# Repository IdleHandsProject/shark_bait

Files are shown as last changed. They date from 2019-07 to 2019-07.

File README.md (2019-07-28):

# SHARK BAIT

Check out the video using the Shark Bait Pumping System:
Shark Bait Video (https://youtu.be/ugRc5jx80yg)

[Marks Channel](https://www.youtube.com/markrober)

For any questions regarding the project or parts please contact SeanHodginsYT@gmail.com

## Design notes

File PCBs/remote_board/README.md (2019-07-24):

# WIND Breakout

## wind makes the feather fly.

WIND is a breakout board for the Adafruit Feather Series to make it easier to fly wire and put together a project with little to no soldering. 

It contains a battery holder for a 18650(I hate loose batteries!), a few buttons, and 5 pin headers for each pin(plus a proto section). There is a power switch connected to the Enable pin(shuts off the regulator), and a voltage divider to the A0 analog 
for monitoring battery voltage.  

This makes it easy to mount in a housing, and wire up different sensors you want to test.

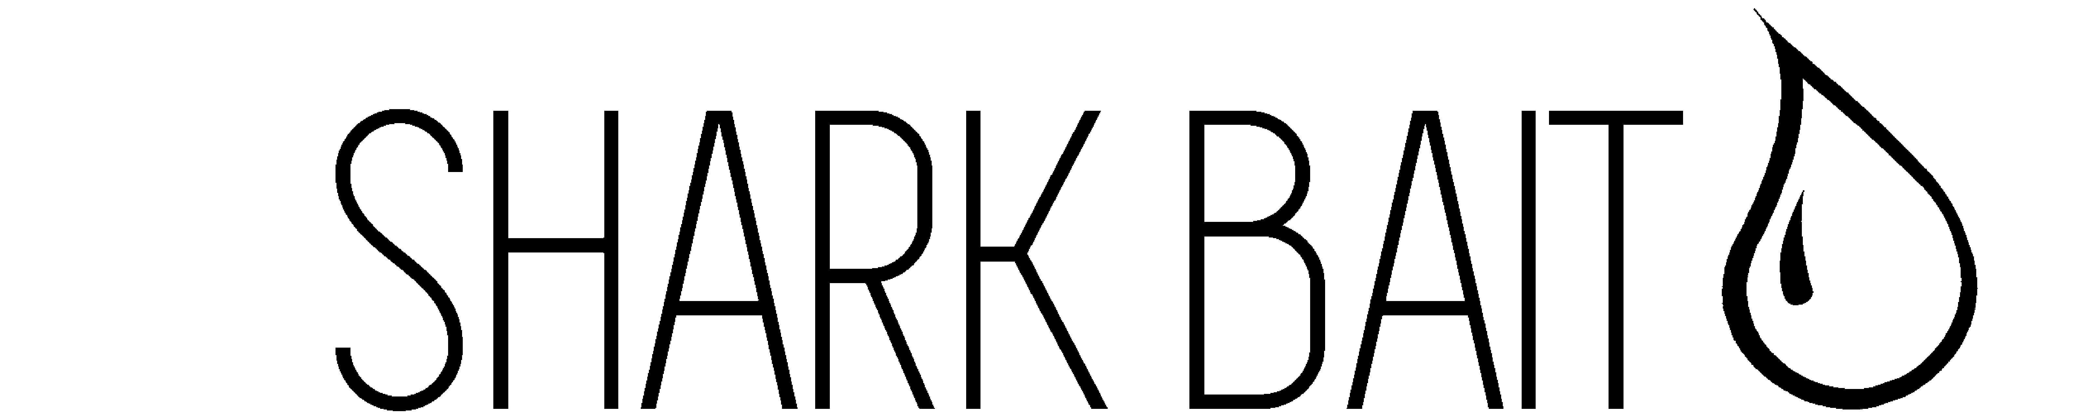
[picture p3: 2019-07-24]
Images/sharkbait.bmp

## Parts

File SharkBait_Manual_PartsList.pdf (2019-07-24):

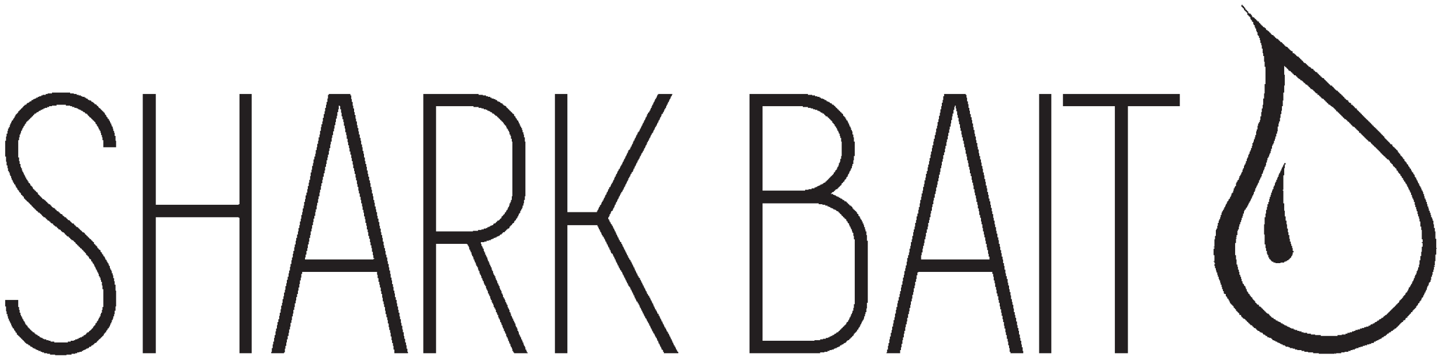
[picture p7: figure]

# Manual and Parts List

## WIRELESS FLUID PUMPING SYSTEM

# PARTS LIST

The following is a list of parts required to build the Shark Bait pumping system. Some parts may vary depending on your requirements.

5 x Adafruit Feather with LoRa - http://bit.ly/sharkbait_feather

4 x Adafruit Motor Wing - http://bit.ly/sharkbait_motor

5 x Waterproof Case - http://bit.ly/sharkbait_case

4 x Peristaltic Pumps 170 ~ 460 mL/min - http://bit.ly/sharkbait_pump

4 x Liquid Container - http://bit.ly/sharkbait_liquid

Silicone 1/4” Tubing - http://bit.ly/sharkbait_tubing

The frames were assembled using various pieces of wood and then mounted to surfboards. You will be required to build your own mounts.

Custom Circuit Boards (Pump and Controller) - Design files available(including BOM), see GitHub link below.

3D Printed Parts - STL Files available in the GitHub link below.

You can find the GitHub that includes the design files and Arduino code here: http://bit.ly/sharkbait_github

For any questions regarding the parts or project, please contact Sean Hodgins. seanhodginsYT@gmail.com

# CONTROLS

## POWER

## ARM

## FLOW SETTINGS

## PRIME

## (REVERSE)

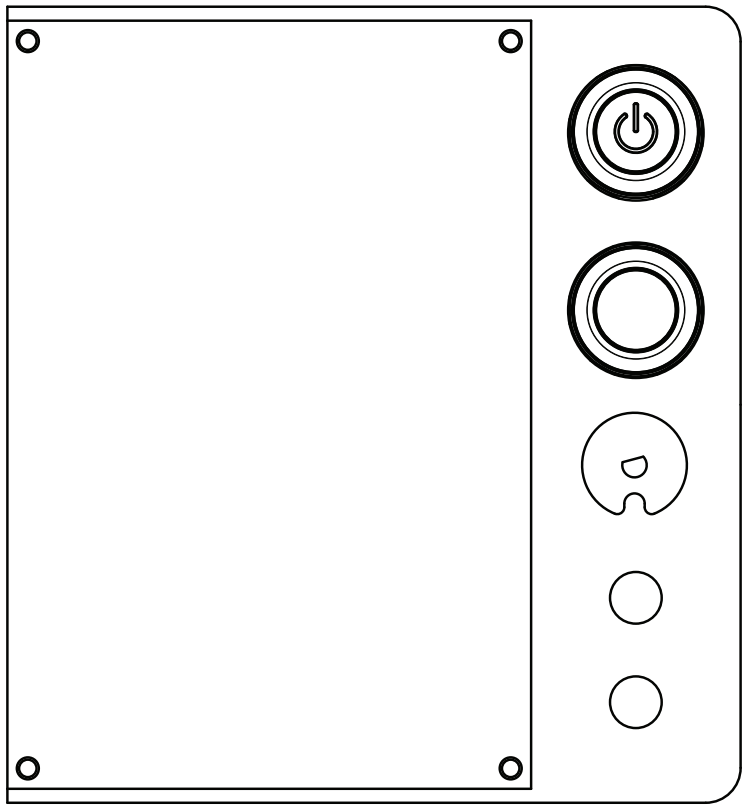
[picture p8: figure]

POWER Button - Direct connection to battery. When in OFF position(UP), no power is provided to the board. POWER button will illuminate when powered.

ARM Button - Will not pump any liquid or respond to remote unless ARM is in ON position(DOWN).

FLOW SETTINGS Knob - 10 settings with an end stop at setting 1(counter clockwise), and 10(clockwise). ARM button illumination will display setting in number of blinks (see next page).

PRIME Button - When held down will cause pump to run forwards(from le port to right port). ARM button will illuminate fully when priming.

REVERSE Button - When held down before holding PRIME will cause the pump to run backwards(from right port to le port). This can be useful for refilling bags(in small amounts).

# SETTINGS

When powering system with ARM Button in the OFF position(UP) system will blink a number of times according to what setting the FLOW Knob is set to (1-10). E.g. Setting 1 will blink once quickly, setting 10 will blink 10 times quickly.

Turn FLOW Knob to desired position coresponding to the flow test amount below. The test amount is in relation to a ONE HOUR test. Each pump of the motor will release approximiately 0.8mL of liquid.
FLOW KNOB SETTING | TEST AMOUNT(mL) | PUMP DELAY(S)
1 | 3.2 900
2 | 25 | 115.2
3 | 50 | 57.6
4 | 100 | 28.8
5 | 250 | 11.5
6 | 500 | 5.8
7 | 750 | 3.8
8 | 1000 | 2.9
9 | 1500 | 1.9
10 | 2000 | 1.4

Once desired flow setting is set, press ARM button to start listening and responding to remote.

ARM button will blink quickly when remote is powered and has received a signal from the remote.

The remote is capable of indicating when the pumps are responding the the signal, and if they are in a pumping state or not.

# MANUAL OVERRIDE

In the rare case the remote is not responding to the pumps, you can put the pumps in MANUAL OVERRIDE mode. This means the pumps will start pumping ONE HOUR aer powering on. Flow rate will be whatever is set at the time the ONE HOUR timer is over. They will not repsond to the remote in MANUAL OVERRIDE mode.

1) First make sure each pump is powered OFF, and ARM button is in OFF Position(UP).

2)Power ON device and select your desired flow setting for each pump.

3) Power OFF device, and set ARM Button to ON Position (DOWN).
4) Power device back ON with ARM button remaining in ON Position. The ARM Button will now blink every second. The flow rate knob can be changed at any time, but no light indication will be available to determine correct setting.
(Its posible to count from one end stop of the knob to the correct position.)

# REMOTE SETTINGS

The remote contains 8 LEDs, 4 LEDs (YELLOW, 5mm) indicate response from the pumps, and 4 LEDs (GREEN, 3mm) indicate an attempt to contact the each pump.

There are two buttons on the side of the remote, POWER and PUMP. The POWER Button will power on the device, the PUMP button will tell any ARMED pumps to begin pumping, when the PUMP button is ON (DOWN).

When the pumps respond to the TX and they are not pumping, the RX LED will blink for that corresponding pump. If the remote PUMP button is ON(down), and the pumps are pumping the RX led will stay illuminated.
The remote will continue to check connectivity to the pumps, and if signal is lost the RX led will turn o. This does not mean the pump has stopped pumping. They will continue to run their test even if the remote is shut o. To stop the motors, turn the PUMP button on the remote to o, while the remote is powered on.
TX | RX/Indication

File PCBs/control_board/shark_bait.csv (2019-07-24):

Id | Designator | Package | Quantity | Designation | Supplier and ref
1 | U4 | SAMD21G18_MOD | 1 | SAMD21_MOD
2 | C2,C4 | C_0402 | 2 | 15pF
3 | C3,C5,C11,C12 | C_0402 | 4 | 0.1uF
4 | C8,C9 | C_0402 | 2 | 1uF
5 | D2 | LED-0603 | 1 | YLED
6 | D1 | LED-0603 | 1 | GLED
7 | R3 | R_0402 | 1 | 10k
8 | R9,R8 | R_0402 | 2 | 1k
9 | Y1 | crystal_smd_3.20x1.50mm2 | 1 | Crystal_Small
10 | D3,D4 | SOD-323 | 2 | BAT20J
11 | J2,J4,J1,J3,J5 | TESTP_1_5 | 5 | TEST_1P
12 | U2 | QFN-48-EP-ST_NoVia | 1 | SAMD21G18
13 | SW4 | switch_kmr2 | 1 | SW_PUSH
14 | U1 | SOT-23-5 | 1 | AP2112K-3.3V
15 | G*** | SH_LOGO_2P5mm | 1 | LOGO

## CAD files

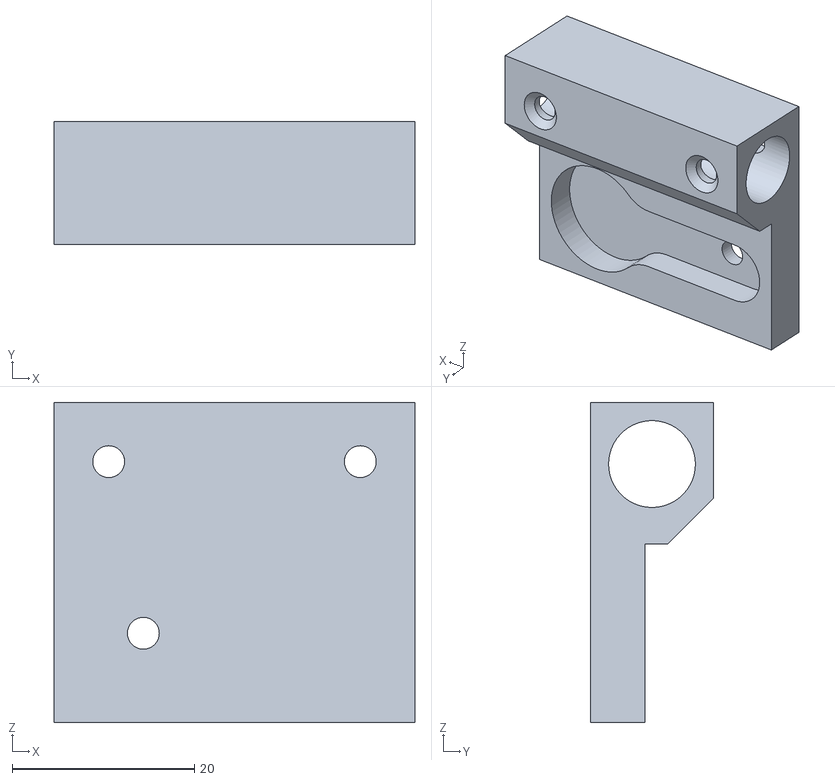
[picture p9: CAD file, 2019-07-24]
STL/Pumps/RodMount.stl
39.6 x 13.5 x 35.1

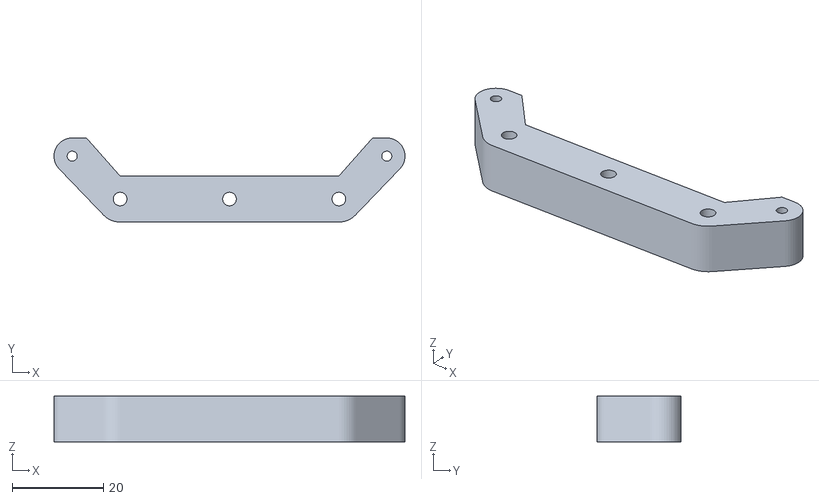
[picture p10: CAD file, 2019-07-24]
STL/Remote/PCBMount.stl
77.0 x 18.5 x 10.0

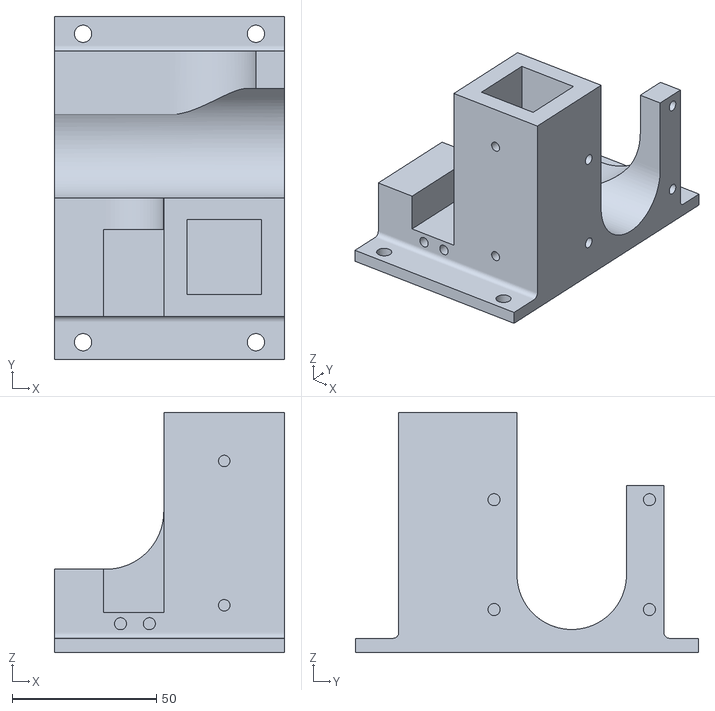
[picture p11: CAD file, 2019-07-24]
STL/Pumps/Mount.stl
80.0 x 119.1 x 83.5

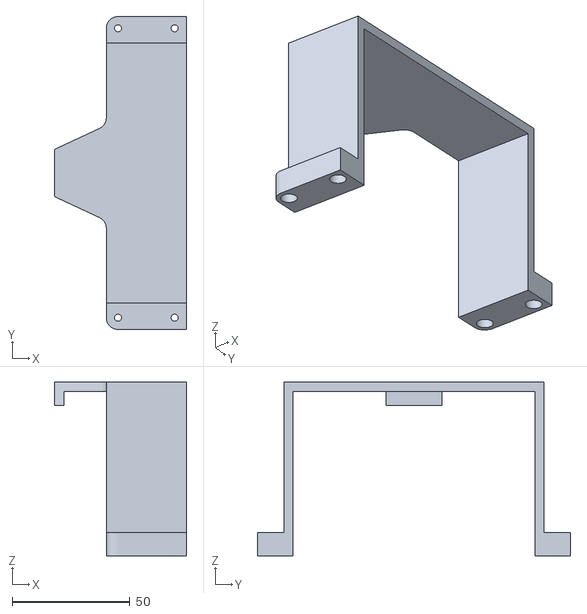
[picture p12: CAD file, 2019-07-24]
STL/Remote/BatteryTieDown.stl
56.1 x 132.8 x 73.8

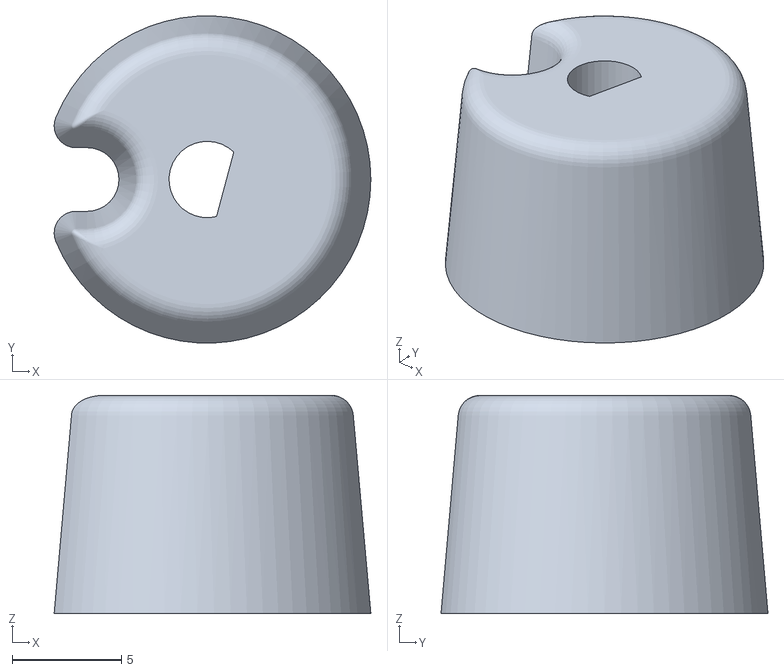
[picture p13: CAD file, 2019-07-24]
STL/Pumps/Knob.stl
14.5 x 15.0 x 10.0

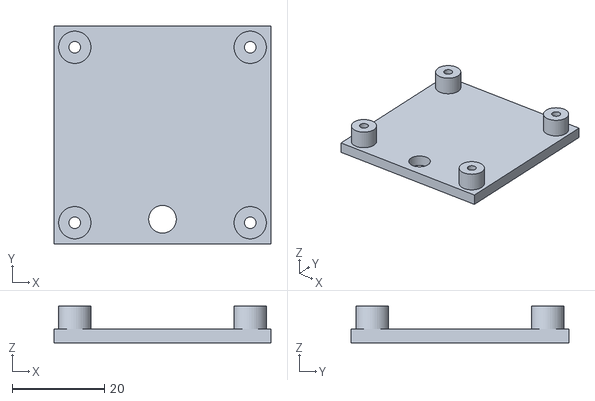
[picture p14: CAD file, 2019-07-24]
STL/Pumps/MotorDriveMount.stl
47.0 x 47.2 x 8.00

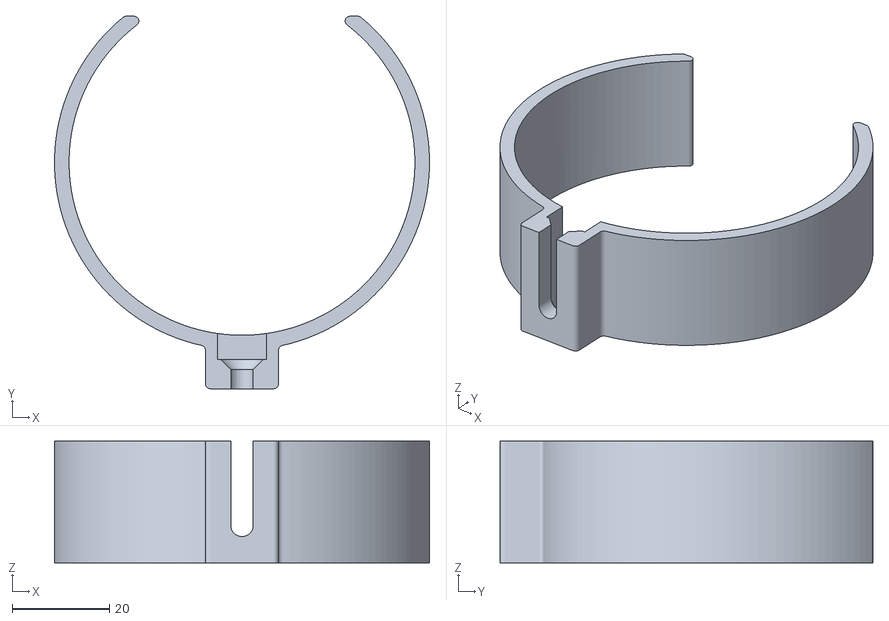
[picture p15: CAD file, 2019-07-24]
STL/Pumps/TubeMount.stl
77.0 x 76.5 x 25.0

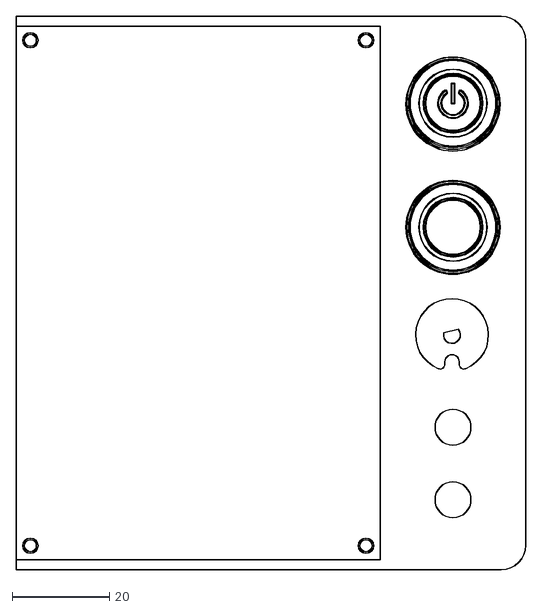
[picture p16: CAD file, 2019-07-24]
STL/Pumps/Drawing1.dxf
105.0 x 114.0

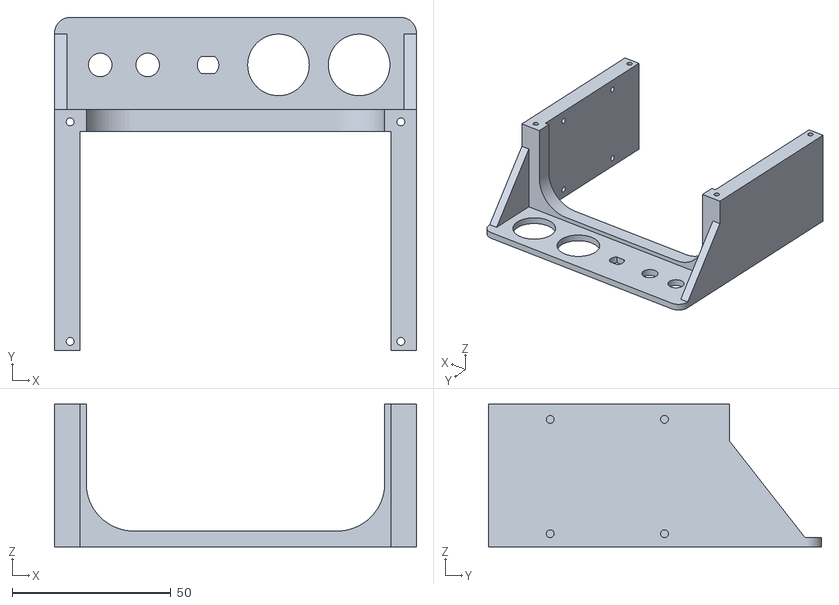
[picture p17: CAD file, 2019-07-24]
STL/Pumps/PCBMount.stl
114.0 x 105.0 x 45.0

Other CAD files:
STL/Pumps/Drawing1.dwg

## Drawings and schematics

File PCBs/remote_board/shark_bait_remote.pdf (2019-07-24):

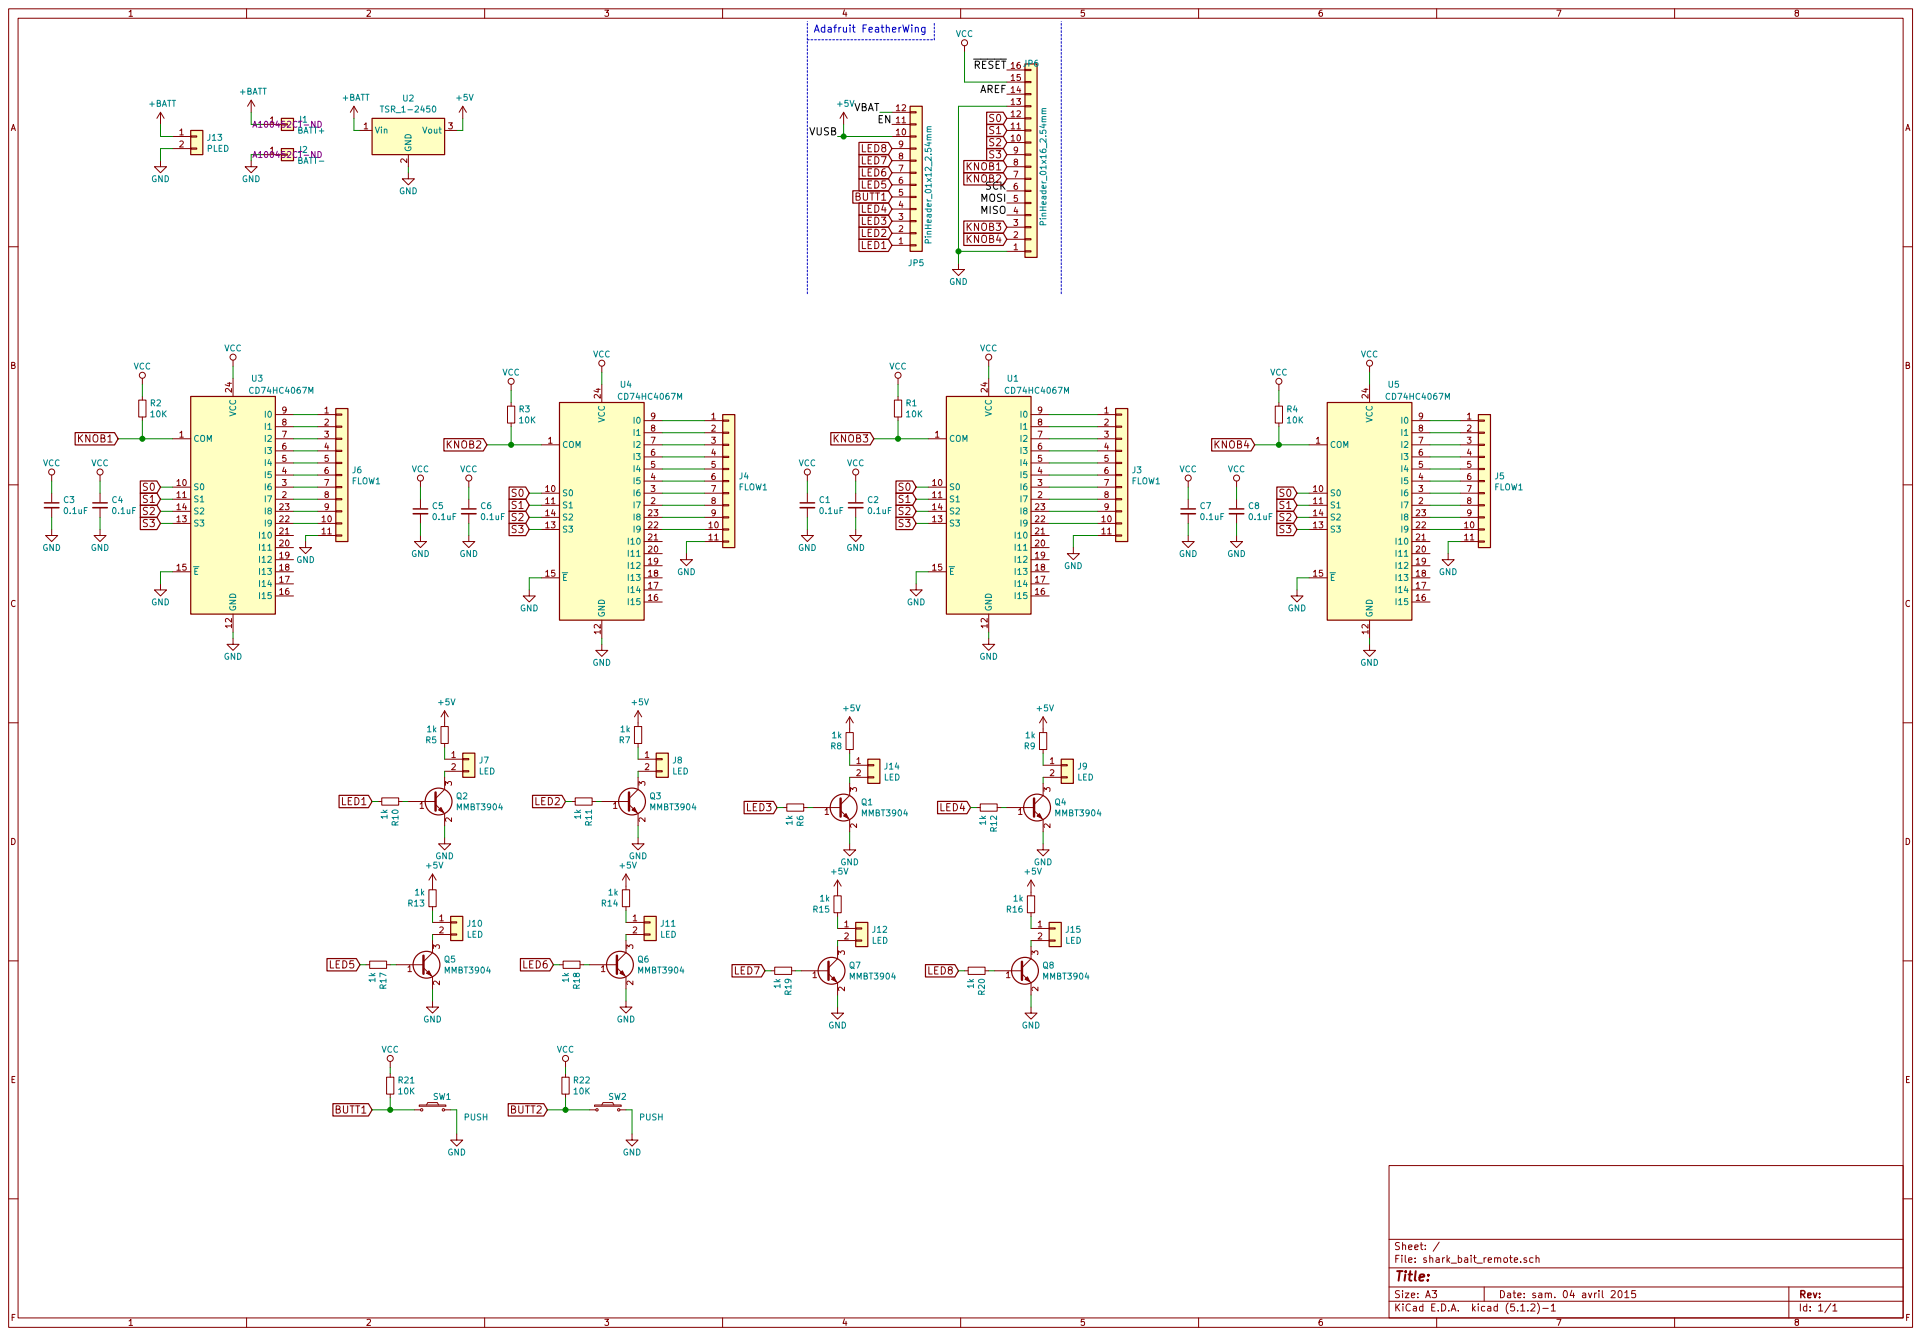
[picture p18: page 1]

GND RESET AREF SCK

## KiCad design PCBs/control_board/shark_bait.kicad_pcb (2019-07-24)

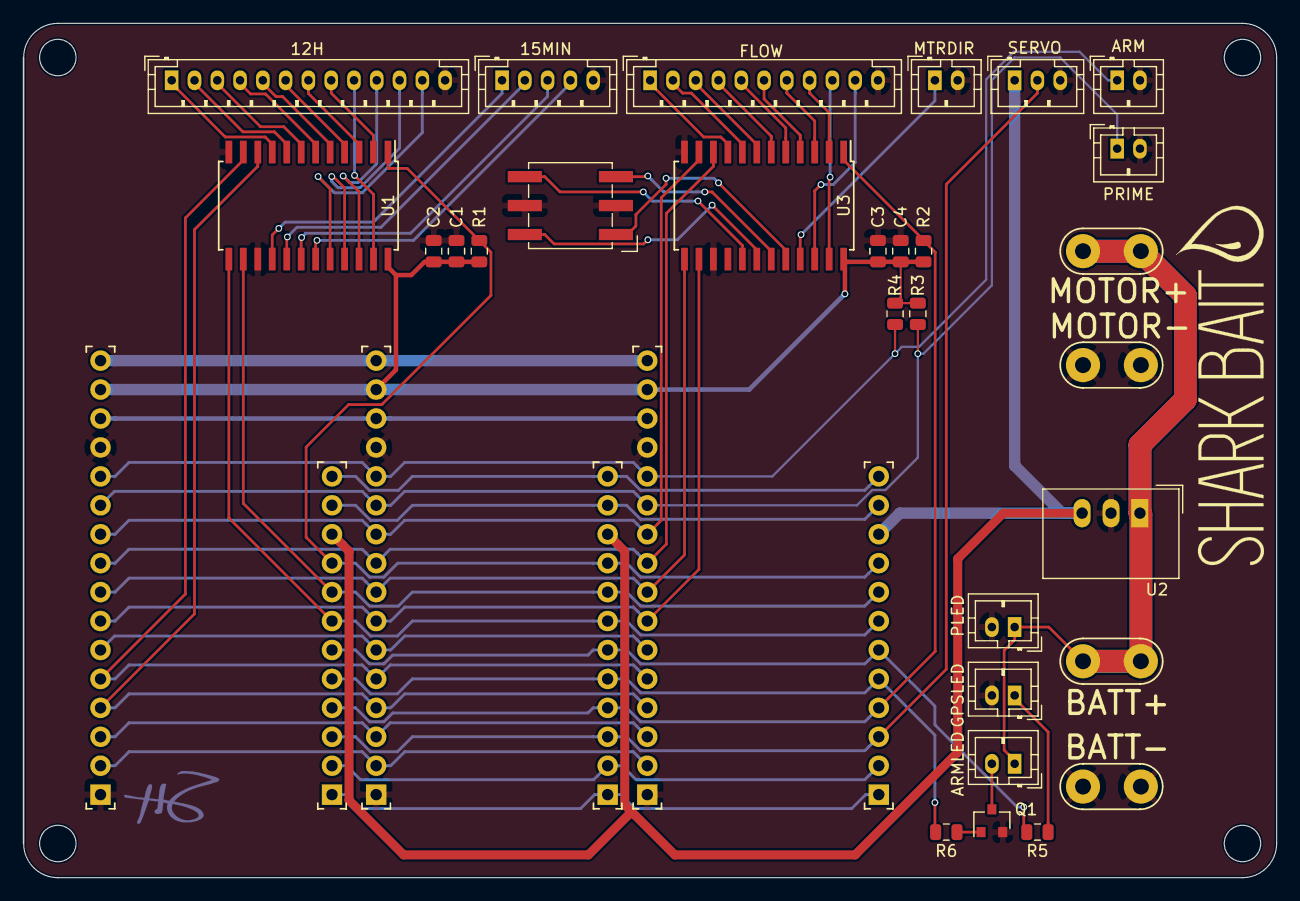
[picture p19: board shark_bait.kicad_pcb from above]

Board: 2 copper layers, 110.0 x 75.0 mm, 38 parts (0 on the bottom side), 62 nets.

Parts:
C1, C2, C3, C4: 0.1uF; C_0805_2012Metric
J1: BATT+; connect_QC_Male
J2: BATT-; connect_QC_Male
J3: 15MIN; JST_PH_B5B-PH-K_1x05_P2.00mm_Vertical
J4: 12H; JST_PH_B13B-PH-K_1x13_P2.00mm_Vertical
J5: MTRDIR; JST_PH_B2B-PH-K_1x02_P2.00mm_Vertical
J6: FLOW; JST_PH_B11B-PH-K_1x11_P2.00mm_Vertical
J7: SERVO; JST_PH_B3B-PH-K_1x03_P2.00mm_Vertical
J8: MOTOR+; connect_QC_Male
J9: MOTOR-; connect_QC_Male
J10: PRIME; JST_PH_B2B-PH-K_1x02_P2.00mm_Vertical
J11: ARM; JST_PH_B2B-PH-K_1x02_P2.00mm_Vertical
J12: GPSLED; JST_PH_B2B-PH-K_1x02_P2.00mm_Vertical
J13: PLED; JST_PH_B2B-PH-K_1x02_P2.00mm_Vertical
J14: ARMLED; JST_PH_B2B-PH-K_1x02_P2.00mm_Vertical
J15: Conn_01x06; Nidec_CS-7
JP1, JP4, JP6: PinHeader_01x16_2.54mm; Conn_PinHeader_1x16_Reduced
JP2, JP3, JP5: PinHeader_01x12_2.54mm; Conn_PinHeader_1x12_Reduced
PCB**: VAL**; PCB_FeatherWing_NoHoles
PCB**#2, PCB**#3: VAL**; PCB_FeatherWing_NoHoles
Q1: MMBT3904; SOT-23
R1, R2, R3, R4: 10K; R_0805_2012Metric
R5: 330; R_0805_2012Metric
R6: 1k; R_0805_2012Metric
U1, U3: CD74HC4067M; SOIC-24W_7.5x15.4mm_P1.27mm
U2: TSR_1-2450; Converter_DCDC_TRACO_TSR-1_THT

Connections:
+5V: J7.1, JP2.10, JP3.10, JP5.10, U2.3
+BATT: J1.1, J8.1, J13.1, J14.1, U2.1
/A2: JP1.10, JP4.10, JP6.10, U3.11
/A3: JP1.9, JP4.9, JP6.9, U3.10
/A4: JP1.8, JP4.8, JP6.8, U3.13
/A5: JP1.7, JP4.7, JP6.7, U3.14
/AREF: JP1.14, JP4.14, JP6.14
/D0: JP1.3, JP4.3, JP6.3
/D1: JP1.2, JP4.2, JP6.2
/D6: JP2.4, JP3.4, JP5.4, R2.2, U3.1
/D11: JP2.7, JP3.7, JP5.7, U1.13
/D12: JP2.8, JP3.8, JP5.8, U1.14
/D13: JP2.9, JP3.9, JP5.9, R1.2, U1.1
/EN: JP2.11, JP3.11, JP5.11
/MISO: JP1.4, JP4.4, JP6.4, U1.10
/MOSI: JP1.5, JP4.5, JP6.5, U1.11
/SCK: JP1.6, JP4.6, JP6.6
/SCL: JP2.2, JP3.2, JP5.2
/SDA: JP2.1, JP3.1, JP5.1
/VBAT: JP2.12, JP3.12, JP5.12
/~RESET: JP1.16, JP4.16, JP6.16
ARM: J11.1, JP1.12, JP4.12, JP6.12, R4.2
ARMLED: JP2.5, JP3.5, JP5.5, R6.2
GND: C1.2, C2.2, C3.2, C4.2, J2.1, J3.5, J4.13, J5.2, J6.11, J7.3, J9.1, J10.2, J11.2, J12.2, J13.2, J15.2, J15.5, JP1.1, JP1.13, JP4.1, JP4.13, JP6.1, JP6.13, Q1.2, U1.12, U1.15, U2.2, U3.12, U3.15
GPSLED: JP2.6, JP3.6, JP5.6, R5.2
unnamed: J3.1, U1.16
unnamed: J3.2, U1.17
unnamed: J3.3, U1.18
unnamed: J3.4, U1.19
unnamed: J4.1, U1.9
unnamed: J4.2, U1.8
unnamed: J4.3, U1.7
unnamed: J4.4, U1.6
unnamed: J4.5, U1.5
unnamed: J4.6, U1.4
unnamed: J4.7, U1.3
unnamed: J4.8, U1.2
unnamed: J4.9, U1.23
unnamed: J4.10, U1.22
unnamed: J4.11, U1.21
unnamed: J4.12, U1.20
unnamed: J5.1, U3.21
unnamed: J6.1, U3.9
unnamed: J6.2, U3.8
unnamed: J6.3, U3.7
unnamed: J6.4, U3.6
unnamed: J6.5, U3.5
unnamed: J6.6, U3.4
unnamed: J6.7, U3.3
unnamed: J6.8, U3.2
unnamed: J6.9, U3.23
unnamed: J6.10, U3.22
unnamed: J12.1, R5.1
unnamed: J14.2, Q1.3
unnamed: J15.1, U3.20
unnamed: J15.3, U3.19
unnamed: J15.4, U3.18
unnamed: J15.6, U3.17
unnamed: Q1.1, R6.1
PRIME: J10.1, JP1.11, JP4.11, JP6.11, R3.2
Servo: J7.2, JP2.3, JP3.3, JP5.3
VCC: C1.1, C2.1, C3.1, C4.1, JP1.15, JP4.15, JP6.15, R1.1, R2.1, R3.1, R4.1, U1.24, U3.24

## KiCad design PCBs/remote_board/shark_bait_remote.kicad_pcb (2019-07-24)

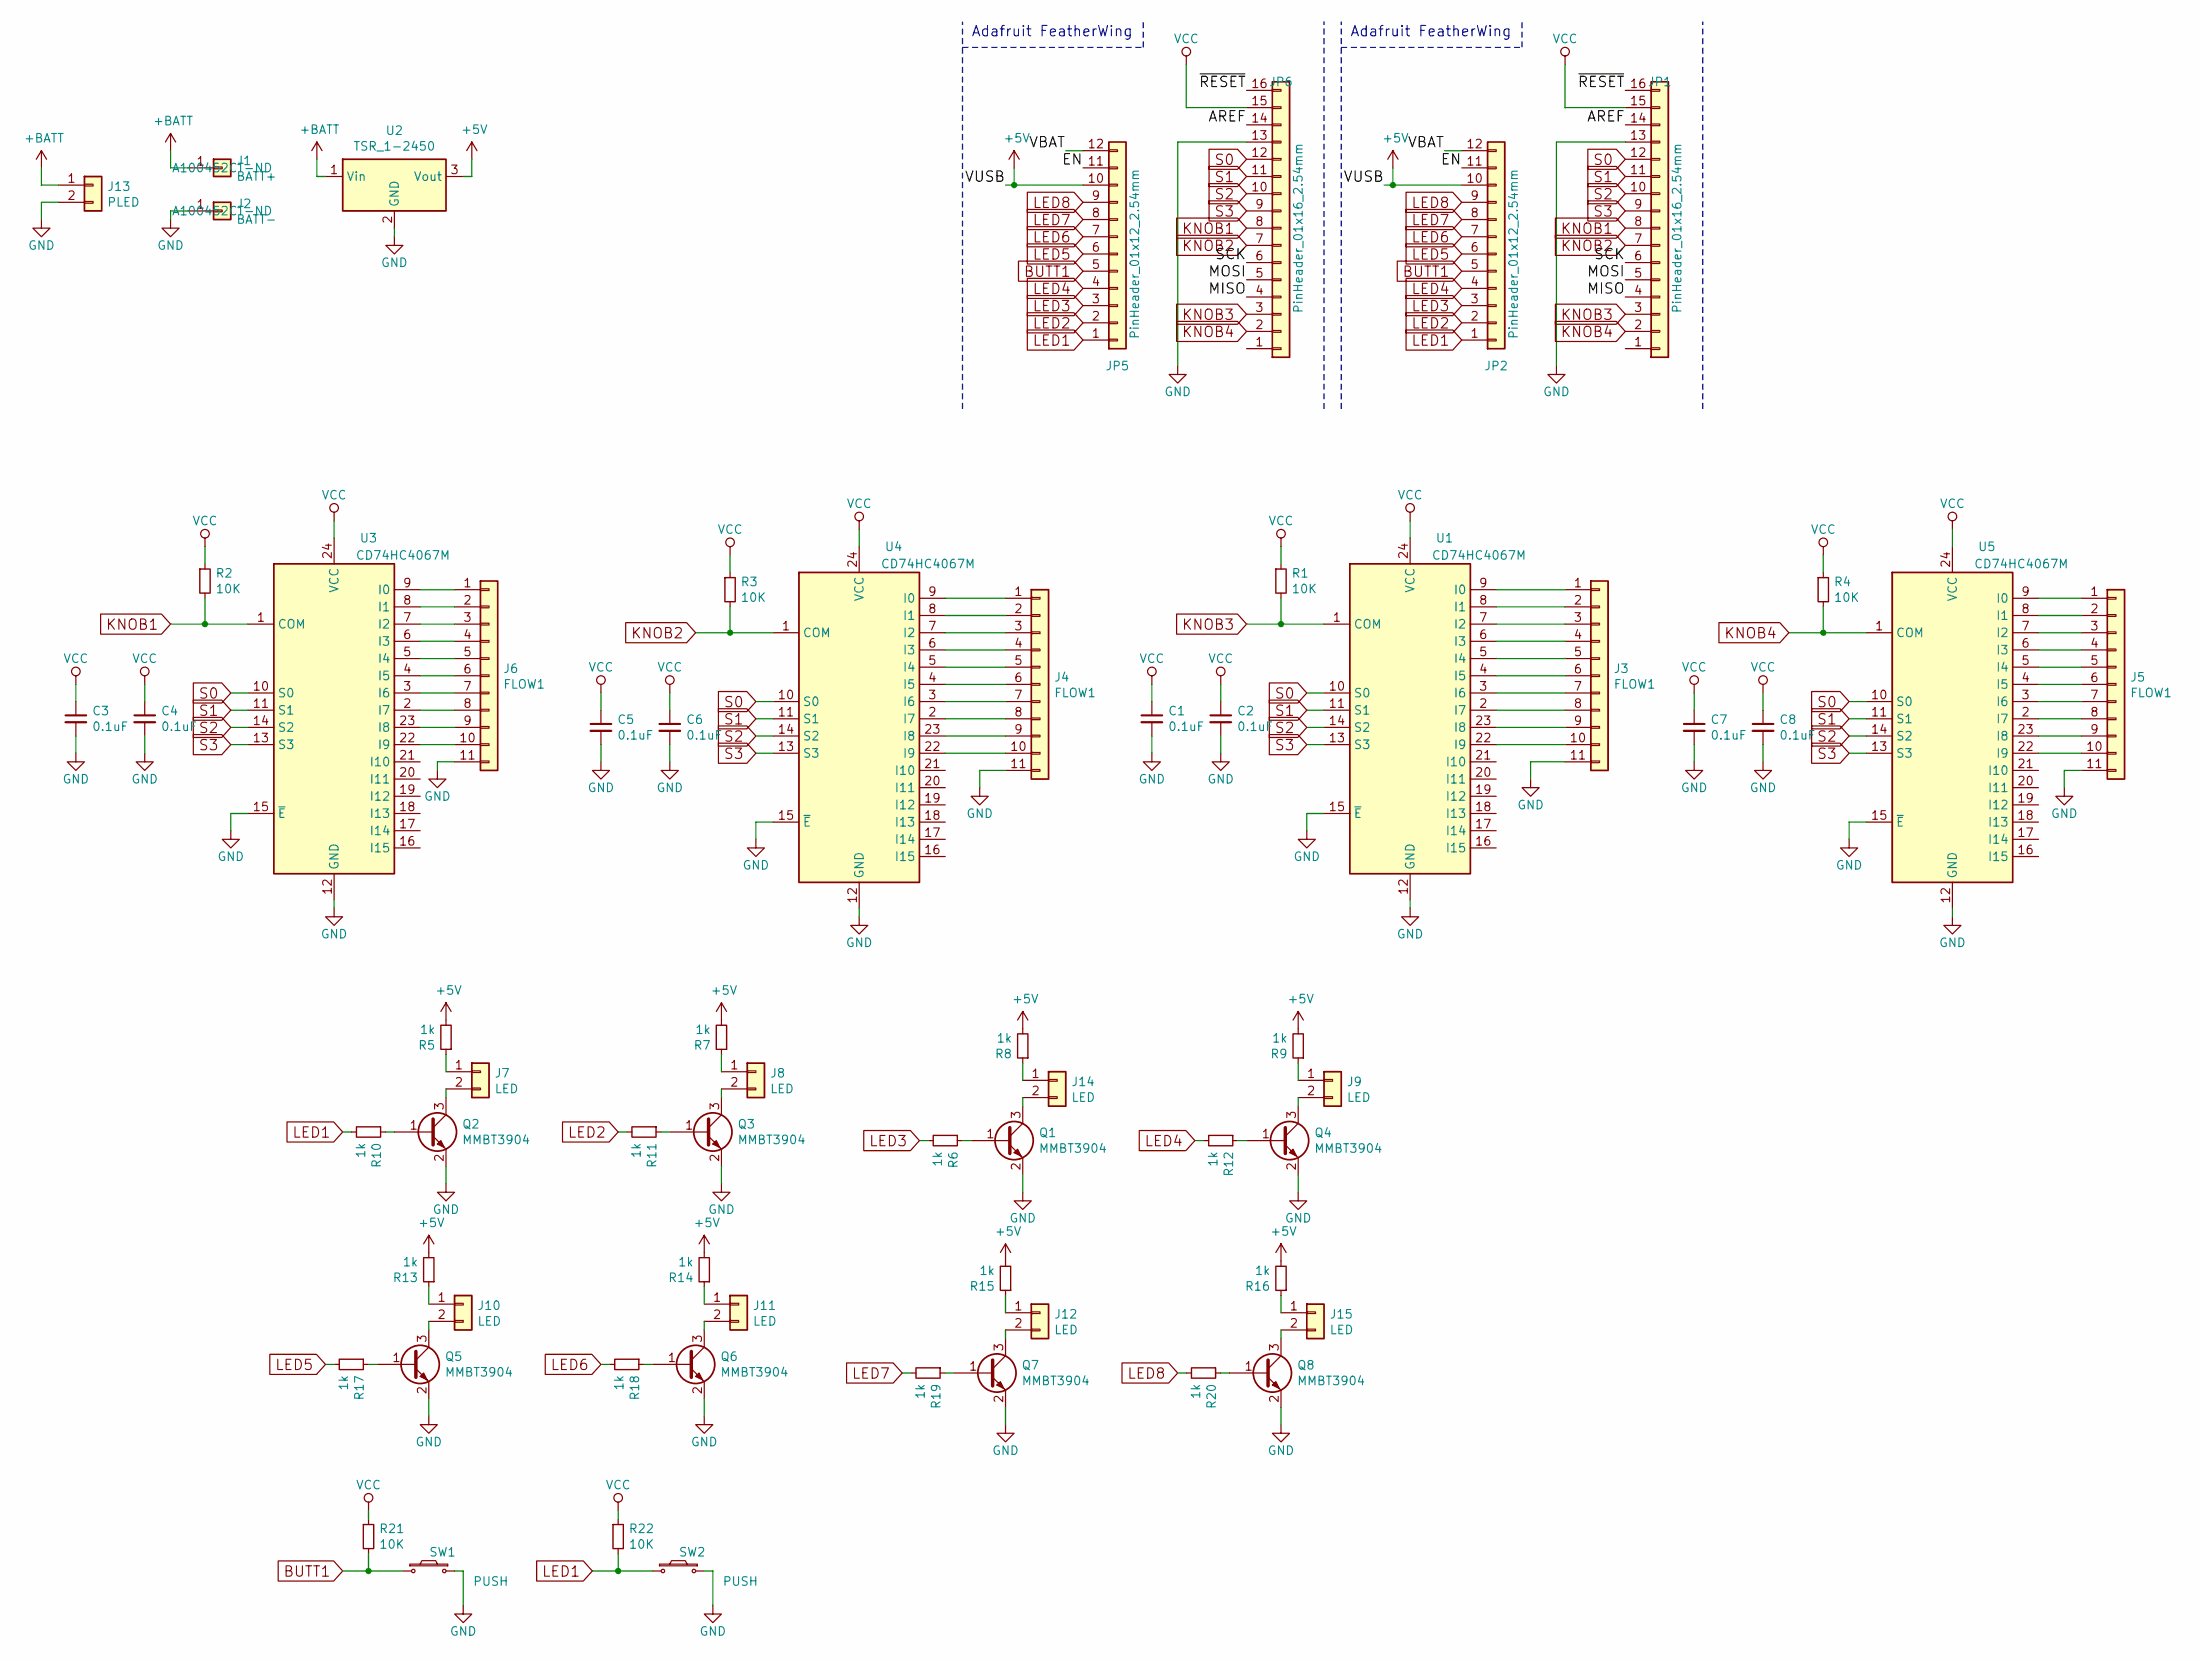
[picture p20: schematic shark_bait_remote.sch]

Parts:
C1, C2, C3, C4, C5, C6, C7, C8: 0.1uF; C_0805_2012Metric
J1: BATT+; connect_QC_Male; Digikey Part No. A100452CT-ND
J2: BATT-; connect_QC_Male; Digikey Part No. A100452CT-ND
J3, J4, J5, J6: FLOW1; JST_PH_B11B-PH-K_1x11_P2.00mm_Vertical
J7, J8, J9, J10, J11, J12, J14, J15: LED; JST_PH_B2B-PH-K_1x02_P2.00mm_Vertical
J13: PLED; JST_PH_B2B-PH-K_1x02_P2.00mm_Vertical
JP1, JP6: PinHeader_01x16_2.54mm; Conn_PinHeader_1x16_Reduced
JP2, JP5: PinHeader_01x12_2.54mm; Conn_PinHeader_1x12_Reduced
Q1, Q2, Q3, Q4, Q5, Q6, Q7, Q8: MMBT3904; SOT-23
R1, R2, R3, R4, R21, R22: 10K; R_0805_2012Metric
R5, R6, R7, R8, R9, R10, R11, R12, R13, R14, R15, R16, R17, R18, R19, R20: 1k; R_0805_2012Metric
SW1, SW2: PUSH; JST_PH_B2B-PH-K_1x02_P2.00mm_Vertical
U1, U3, U4, U5: CD74HC4067M; SOIC-24W_7.5x15.4mm_P1.27mm; Digikey Part No. 296-29408-1-ND
U2: TSR_1-2450; Converter_DCDC_TRACO_TSR-1_THT

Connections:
+5V: JP2.10, JP5.10, R5.2, R7.2, R8.2, R9.2, R13.2, R14.2, R15.2, R16.2, U2.3 (Vout)
+BATT: J1.1, J13.1, U2.1 (Vin)
/AREF: JP1.14, JP6.14
/EN: JP2.11, JP5.11
/MISO: JP1.4, JP6.4
/MOSI: JP1.5, JP6.5
/SCK: JP1.6, JP6.6
/VBAT: JP2.12, JP5.12
/~RESET: JP1.16, JP6.16
BUTT1: JP2.5, JP5.5, R21.2, SW1.1
GND: C1.2, C2.2, C3.2, C4.2, C5.2, C6.2, C7.2, C8.2, J2.1, J3.11, J4.11, J5.11, J6.11, J13.2, JP1.1, JP1.13, JP6.1, JP6.13, Q1.2 (E), Q2.2 (E), Q3.2 (E), Q4.2 (E), Q5.2 (E), Q6.2 (E), Q7.2 (E), Q8.2 (E), SW1.2, SW2.2, U1.12 (GND), U1.15 (~E), U2.2 (GND), U3.12 (GND), U3.15 (~E), U4.12 (GND), U4.15 (~E), U5.12 (GND), U5.15 (~E)
KNOB1: JP1.8, JP6.8, R2.2, U3.1 (COM)
KNOB2: JP1.7, JP6.7, R3.2, U4.1 (COM)
KNOB3: JP1.3, JP6.3, R1.2, U1.1 (COM)
KNOB4: JP1.2, JP6.2, R4.2, U5.1 (COM)
LED1: JP2.1, JP5.1, R10.2, R22.2, SW2.1
LED2: JP2.2, JP5.2, R11.2
LED3: JP2.3, JP5.3, R6.2
LED4: JP2.4, JP5.4, R12.2
LED5: JP2.6, JP5.6, R17.2
LED6: JP2.7, JP5.7, R18.2
LED7: JP2.8, JP5.8, R19.2
LED8: JP2.9, JP5.9, R20.2
unnamed: J3.1, U1.9 (I0)
unnamed: J3.2, U1.8 (I1)
unnamed: J3.3, U1.7 (I2)
unnamed: J3.4, U1.6 (I3)
unnamed: J3.5, U1.5 (I4)
unnamed: J3.6, U1.4 (I5)
unnamed: J3.7, U1.3 (I6)
unnamed: J3.8, U1.2 (I7)
unnamed: J3.9, U1.23 (I8)
unnamed: J3.10, U1.22 (I9)
unnamed: J4.1, U4.9 (I0)
unnamed: J4.2, U4.8 (I1)
unnamed: J4.3, U4.7 (I2)
unnamed: J4.4, U4.6 (I3)
unnamed: J4.5, U4.5 (I4)
unnamed: J4.6, U4.4 (I5)
unnamed: J4.7, U4.3 (I6)
unnamed: J4.8, U4.2 (I7)
unnamed: J4.9, U4.23 (I8)
unnamed: J4.10, U4.22 (I9)
unnamed: J5.1, U5.9 (I0)
unnamed: J5.2, U5.8 (I1)
unnamed: J5.3, U5.7 (I2)
unnamed: J5.4, U5.6 (I3)
unnamed: J5.5, U5.5 (I4)
unnamed: J5.6, U5.4 (I5)
unnamed: J5.7, U5.3 (I6)
unnamed: J5.8, U5.2 (I7)
unnamed: J5.9, U5.23 (I8)
unnamed: J5.10, U5.22 (I9)
unnamed: J6.1, U3.9 (I0)
unnamed: J6.2, U3.8 (I1)
unnamed: J6.3, U3.7 (I2)
unnamed: J6.4, U3.6 (I3)
unnamed: J6.5, U3.5 (I4)
unnamed: J6.6, U3.4 (I5)
unnamed: J6.7, U3.3 (I6)
unnamed: J6.8, U3.2 (I7)
unnamed: J6.9, U3.23 (I8)
unnamed: J6.10, U3.22 (I9)
unnamed: J7.1, R5.1
unnamed: J7.2, Q2.3 (C)
unnamed: J8.1, R7.1
unnamed: J8.2, Q3.3 (C)
unnamed: J9.1, R9.1
unnamed: J9.2, Q4.3 (C)
unnamed: J10.1, R13.1
unnamed: J10.2, Q5.3 (C)
unnamed: J11.1, R14.1
unnamed: J11.2, Q6.3 (C)
unnamed: J12.1, R15.1
unnamed: J12.2, Q7.3 (C)
unnamed: J14.1, R8.1
unnamed: J14.2, Q1.3 (C)
unnamed: J15.1, R16.1
unnamed: J15.2, Q8.3 (C)
unnamed: Q1.1 (B), R6.1
unnamed: Q2.1 (B), R10.1
unnamed: Q3.1 (B), R11.1
unnamed: Q4.1 (B), R12.1
unnamed: Q5.1 (B), R17.1
unnamed: Q6.1 (B), R18.1
unnamed: Q7.1 (B), R19.1
unnamed: Q8.1 (B), R20.1
S0: JP1.12, JP6.12, U1.10 (S0), U3.10 (S0), U4.10 (S0), U5.10 (S0)
S1: JP1.11, JP6.11, U1.11 (S1), U3.11 (S1), U4.11 (S1), U5.11 (S1)
S2: JP1.10, JP6.10, U1.14 (S2), U3.14 (S2), U4.14 (S2), U5.14 (S2)
S3: JP1.9, JP6.9, U1.13 (S3), U3.13 (S3), U4.13 (S3), U5.13 (S3)
VCC: C1.1, C2.1, C3.1, C4.1, C5.1, C6.1, C7.1, C8.1, JP1.15, JP6.15, R1.1, R2.1, R3.1, R4.1, R21.1, R22.1, U1.24 (VCC), U3.24 (VCC), U4.24 (VCC), U5.24 (VCC)

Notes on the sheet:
Adafruit FeatherWing

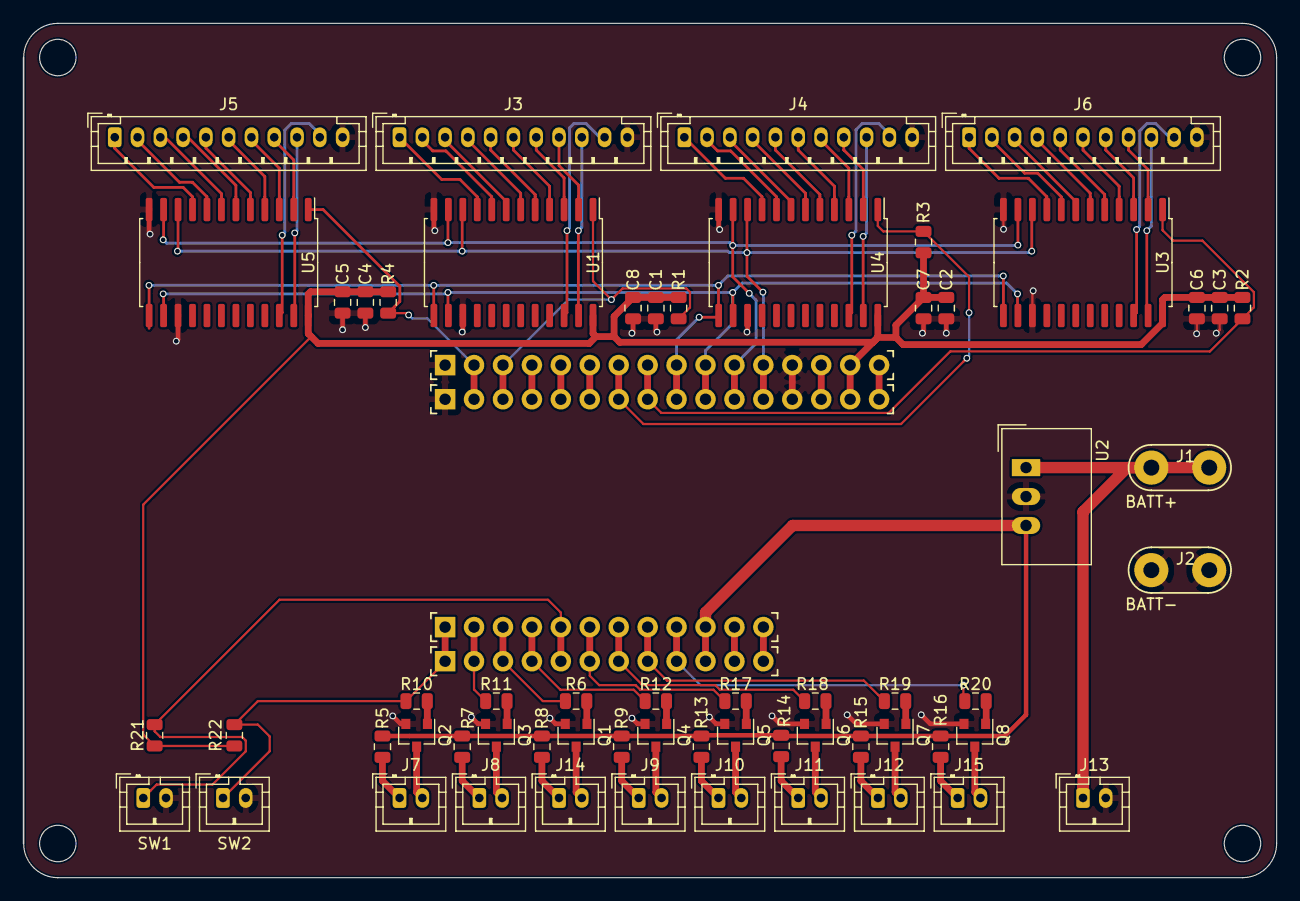
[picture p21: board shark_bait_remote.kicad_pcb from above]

Board: 2 copper layers, 110.0 x 75.0 mm, 65 parts (0 on the bottom side), 92 nets.

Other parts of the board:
PCB**: VAL**; PCB_FeatherWing_NoHoles

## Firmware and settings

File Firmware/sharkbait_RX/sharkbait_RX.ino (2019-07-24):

/*Shark Bait Firmware RX
   Program recieves a signal from the remote to start or stop the shark bait
   It recieves a value asking if that is the currect receiver, and also a "Flow" value selected by the user.
*/


#define FEATHERMOTOR
//#define L298N

#include <SPI.h>
#include <RH_RF95.h>
#include <Servo.h>

#ifdef FEATHERMOTOR
#include <Wire.h>
#include <Adafruit_MotorShield.h>
Adafruit_MotorShield AFMS = Adafruit_MotorShield();
Adafruit_DCMotor *pump = AFMS.getMotor(1);
#endif

//#define TESTKNOB
//#define DEBUG*

Servo myservo;

#define FeatherLORA
//#define ModuleLORA

//LORA Module
#ifdef ModuleLORA
#define RFM95_CS 13
#define RFM95_RST 11
#define RFM95_INT 12
#endif
// LORA Feather
#ifdef FeatherLORA
#define RFM95_CS 8
#define RFM95_RST 4
#define RFM95_INT 3
#endif

#define MOTORA 20
#define MOTORB 21

// Change to 434.0 or other frequency, must match RX's freq!
#define RF95_FREQ 915.0

// Singleton instance of the radio driver
RH_RF95 rf95(RFM95_CS, RFM95_INT);

// Blinky on receipt
#define LED 13

int RecNum = 0;
int state = 0; // 0 = off, 1 = pumping
int laststate = 0;
int flowSetting = 0;  // Flow Settings(0-9)
int lastflow = 0;
int flowDelay = 60000;

unsigned long startTime = 0;
unsigned long pumpTime = 0;

#define PRIME A1
#define ARM A0
#define ARMLED 9
#define SERVO 5
#define LIMIT 5
#define MINUTES 60000
#define SECONDS 1000
#define PUMPTIME 100

int s[4] = {A3, A2, A5, A4};
int com = 6;

void setup()
{
  pinMode(LED, OUTPUT);
  pinMode(RFM95_RST, OUTPUT);
  digitalWrite(RFM95_RST, HIGH);
  pinMode(ARM, INPUT_PULLUP);
  pinMode(ARMLED, OUTPUT);
  digitalWrite(ARMLED, LOW);
  pinMode(PRIME, INPUT_PULLUP);
  pinMode(com, INPUT);
  for (int x = 0; x < 4; x++) {
    pinMode(s[x], OUTPUT);
    digitalWrite(s[x], LOW);
  }

#ifdef L298N
  pinMode(MOTORB, OUTPUT);
  digitalWrite(MOTORB, LOW);
  pinMode(MOTORA, OUTPUT);
  digitalWrite(MOTORA, LOW);
#endif

  Serial.begin(115200);
#ifdef FEATHERMOTOR
  AFMS.begin();
  pump->setSpeed(255);
  pump->run(FORWARD);
  // turn on motor
  pump->run(RELEASE);
#endif
  //while (!Serial) {
  //  delay(1);
  //}
  //delay(100);
  // Check what number the sensor is set to (with the Rotary DIP);
  RecNum = checkRec();
  myservo.attach(SERVO);
  myservo.write(90);
  delay(500);
  myservo.detach();


#ifdef TESTKNOB
  int lasttestflow = 0;
  while (1) {
    int testflow = checkFlow();
    if (lasttestflow != testflow) {
      Serial.println(testflow);
      lasttestflow = testflow;
    }

    delay(100);
  }
#endif


  // IF YOU START WITH ARM SWITCH ACTIVE IT WILL MANUALLY OVERRIDE THE RF SIGNAL AND START PUMPING IN ONE HOUR DEPENDING ON SET FLOW RATE
  int OVERRIDE = !(digitalRead(ARM));
  unsigned int sorTime = millis();
  unsigned int eorTime = millis();
  unsigned int lorTime = millis();
  unsigned int porTime = millis();
  int overtime = 60000 * 60;
  //int overtime = 5000;
  int pumping = 0;
  int flashtime = 500;
  byte light = 0;
  int flow = checkFlow();
  setFlow(flow);
  Serial.println("Checking Manual Override Switch");
  while ( OVERRIDE == 1) {

    OVERRIDE = !(digitalRead(ARM));
    eorTime = millis();
    if (eorTime - lorTime > flashtime) {
      light = !(light);
      digitalWrite(ARMLED, light);
      lorTime = millis();
      Serial.println(light);
      Serial.println(overtime - eorTime);
    }
    if (pumping == 0) {
      if (eorTime - sorTime > overtime) {
        pumping = 1;
        spinPump();
        spinPump();
      }
    }
    while (pumping == 1) {
      flowSetting = checkFlow();
      setFlow(flowSetting);
      eorTime = millis();
      if (eorTime - porTime > flowDelay) {
        spinPump();
        porTime = millis();
        if (porTime > 120 * MINUTES){
          Serial.println("Test Done");
          while (1);
        }
      }
    }

  }

  Serial.println("Feather LoRa RX Test!");

  // manual reset
  digitalWrite(RFM95_RST, LOW);
  delay(10);
  digitalWrite(RFM95_RST, HIGH);
  delay(10);

  while (!rf95.init()) {
    Serial.println("LoRa radio init failed");
    while (1);
  }
  Serial.println("LoRa radio init OK!");

  // Defaults after init are 434.0MHz, modulation GFSK_Rb250Fd250, +13dbM
  if (!rf95.setFrequency(RF95_FREQ)) {
    Serial.println("setFrequency failed");
    while (1);
  }
  //Serial.print("Set Freq to: "); Serial.println(RF95_FREQ);

  // Defaults after init are 434.0MHz, 13dBm, Bw = 125 kHz, Cr = 4/5, Sf = 128chips/symbol, CRC on

  // The default transmitter power is 13dBm, using PA_BOOST.
  // If you are using RFM95/96/97/98 modules which uses the PA_BOOST transmitter pin, then
  // you can set transmitter powers from 5 to 23 dBm:
  rf95.setTxPower(23, false);
  //attachInterrupt(PRIME, Prime, LOW);
}

void loop()
{
  int prime = digitalRead(PRIME);
  while (prime == 0) {
    prime = digitalRead(PRIME);
    Prime();
  }
  flowSetting = checkFlow();
  for (int z = 0; z < flowSetting + 1; z++) {
    digitalWrite(ARMLED, HIGH);
    delay(100);
    digitalWrite(ARMLED, LOW);
    delay(100);
  }
  delay(1000);
  int armed = !(digitalRead(ARM));

  while (armed == 1) {
    if (rf95.available()) {
      // Should be a message for us now
      uint8_t buf[RH_RF95_MAX_MESSAGE_LEN];
      uint8_t len = sizeof(buf);

      if (rf95.recv(buf, &len))
      {
        digitalWrite(ARMLED, HIGH);
        //RH_RF95::printBuffer("Received: ", buf, len);
        Serial.print("Got: ");
        Serial.println((char*)buf);
        Serial.print("RSSI: ");
        Serial.println(rf95.lastRssi(), DEC);

        // Message for this number.
        if (char(buf[0]) == RecNum + 48) {
          //myservo.attach(SERVO);
          //myservo.write(0);
          //delay(500);
          //myservo.detach();
          state = buf[2] - 48;
          flowSetting = buf[4] - 48;
          if (flowSetting == -16) {
            flowSetting = checkFlow();
            setFlow(flowSetting);
          }
          String sendStr = String(RecNum);
          sendStr += ",";
          sendStr += String(state);
          sendStr += ",";
          sendStr += String(flowSetting);
          char sendBuf[6];
          sendStr.toCharArray(sendBuf, 6);
          rf95.send((uint8_t *)sendBuf, sizeof(sendBuf));
          rf95.waitPacketSent();
          Serial.println("Taking Commands:");
          Serial.print("State: ");
          Serial.println(state);
          Serial.print("Flow Setting: ");
          Serial.println(flowSetting);
          Serial.println("Sent a reply");
        }
        else {
          Serial.println("Message for someone else...");
        }
        digitalWrite(ARMLED, LOW);
      }
      else
      {
        Serial.println("Receive failed");
      }
    }

    if (state != laststate) {
      setServo(state);
      setFlow(flowSetting);
      laststate = state;
      startTime = millis();
      if (state == 1) {
        Serial.println("Starting Pump Timer");
        spinPump();
        spinPump();
      }
    }

    if (state == 1) {
      pumpTime = millis();
      if (pumpTime - startTime > flowDelay) {
        spinPump();
        startTime = millis();
      }
    }
    armed = !(digitalRead(ARM));
  }
}


byte checkTime(unsigned long stime, unsigned long ptime) {
  unsigned long timer = ptime - stime;
  byte timetopump = 0;
  if (timer > flowDelay) {
    timetopump = 1;
  }
  return timetopump;
}

byte checkMuxPin(int pin) {
  for (int i = 0; i < 4; i++) {
    byte state = bitRead(pin, i);
    digitalWrite(s[i], state);
#ifdef DEBUG
    Serial.print(state);
#endif
  }
#ifdef DEBUG
  Serial.print(",");
  Serial.println(pin);
#endif
  byte check = digitalRead(com);
  return check;
}


int checkRec() {
  int Rec = 0;
  for (int i = 11; i < 15; i++) {
    byte val = checkMuxPin(i);
    if (val == 0) {
      Rec = i - 11;
    }
  }
#ifdef DEBUG
  Serial.print("Receiver Number: ");
  Serial.println(Rec);
#endif
  return Rec;
}

int checkFlow() {
  int setting = 0;
  for (int i = 0; i < 10; i++) {
    byte val = checkMuxPin(i);
    if (val == 0) {
      setting = i;
    }
  }
#ifdef DEBUG
  Serial.print("Flow Setting: ");
  Serial.println(setting);
#endif
  return setting;
}

int setFlow(int flowsetting) {
  switch (flowsetting) {
    case 0:
      flowDelay = 15 * MINUTES;
      break;
    case 1:
      flowDelay = 115200;  
      break;
    case 2:
      flowDelay = 57600;
      break;
    case 3:
      flowDelay = 28800;
      break;
    case 4:
      flowDelay = 11520;
      break;
    case 5:
      flowDelay = 5760;
      break;
    case 6:
      flowDelay = 3840;
      break;
    case 7:
      flowDelay = 2880;
      break;
    case 8:
      flowDelay = 1920;
      break;
    case 9:
      flowDelay = 1440;
      break;
    default:
      break;
  }
}

byte checkDir() {
  byte dir = checkMuxPin(10);
  return dir;
}

void setServo(int val) {
  if (val == 1) {
    myservo.attach(SERVO);
    myservo.write(0);
    delay(500);
    myservo.detach();
  }
  else {
    myservo.attach(SERVO);
    myservo.write(90);
    delay(500);
    myservo.detach();
  }
}

void spinPump() { //Spins the pump one pulse
  Serial.println("Spinning Pump");
#ifdef L298N
  digitalWrite(MOTORB, HIGH);
  digitalWrite(MOTORA, LOW);
#endif
#ifdef FEATHERMOTOR
  pump->run(FORWARD);
#endif
  delay(PUMPTIME);
#ifdef L298N
  digitalWrite(MOTORB, LOW);
  digitalWrite(MOTORA, LOW);
#endif
#ifdef FEATHERMOTOR
  pump->run(RELEASE);
#endif
}

void Prime() {
  byte dir = checkDir();
  if (dir == 0) {
#ifdef L298N
    digitalWrite(MOTORA, HIGH);
    digitalWrite(MOTORB, LOW);
#endif
#ifdef FEATHERMOTOR
    pump->run(BACKWARD);
#endif
    Serial.println("Reverse");
  }
  else {
#ifdef L298N
    digitalWrite(MOTORB, HIGH);
    digitalWrite(MOTORA, LOW);
#endif
#ifdef FEATHERMOTOR
    pump->run(FORWARD);
#endif
  }
  int button = digitalRead(PRIME);
  while (button == 0) {
    digitalWrite(ARMLED, HIGH);
    button = digitalRead(PRIME);
    Serial.println("PRIMING Pump");
    delay(100);
    digitalWrite(ARMLED, LOW);
  }
#ifdef L298N
  digitalWrite(MOTORB, LOW);
  digitalWrite(MOTORA, LOW);
#endif
#ifdef FEATHERMOTOR
  pump->run(RELEASE);
#endif

}

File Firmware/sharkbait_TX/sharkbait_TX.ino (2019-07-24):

/* Shark Bair Firmware TX
    Program sends a signal to each of the 4 pumping stations and checks to see if they are running
    It will also send a "Flow" value to make sure they are pumping at the correct rate.
*/
#include <SPI.h>
#include <RH_RF95.h>


#define FeatherLORA
//#define ModuleLORA

//LORA Module
#ifdef ModuleLORA
#define RFM95_CS 13
#define RFM95_RST 11
#define RFM95_INT 12
#endif
// LORA Feather
#ifdef FeatherLORA
#define RFM95_CS 8
#define RFM95_RST 4
#define RFM95_INT 3
#endif

#define TESTKNOB
#define BUTT1 9

int s[4] = {14, 15, 16, 17};
int b[4] = {18, 19, 0, 1};

int sLED[4] = {20, 21, 5, 6};
int tLED[4] = {10, 11, 12, 13};

int f[4] = {0, 0, 0, 0};


// Change to 434.0 or other frequency, must match RX's freq!
#define RF95_FREQ 915.0

int state = 0;

// Singleton instance of the radio driver
RH_RF95 rf95(RFM95_CS, RFM95_INT);

void setup()
{
  pinMode(RFM95_RST, OUTPUT);
  digitalWrite(RFM95_RST, HIGH);
  pinMode(BUTT1, INPUT);
  //pinMode(8, OUTPUT);

  for (int y = 0; y < 3; y++) {
    pinMode(sLED[y], OUTPUT);
    pinMode(tLED[y], OUTPUT);
    digitalWrite(sLED[y], HIGH);
    digitalWrite(tLED[y], HIGH);
    pinMode(b[y], INPUT);
    pinMode(s[y], OUTPUT);
    digitalWrite(s[y], LOW);
    delay(300);
  }
  delay(1000);
  for (int j = 0; j < 3; j++) {
    digitalWrite(sLED[j], LOW);
    digitalWrite(tLED[j], LOW);
  }

  Serial.begin(115200);
  //while (!Serial) {
  //  delay(1);
  //}
#ifdef TESTKNOB
  int lasttestflow = 0;
  while (1) {
    int testflow = checkFlow(0);
    if (lasttestflow != testflow) {
      Serial.println(testflow);
      lasttestflow = testflow;
    }
    delay(100);
  }
#endif
  delay(100);

  Serial.println("Feather LoRa TX Test!");

  // manual reset
  digitalWrite(RFM95_RST, LOW);
  delay(10);
  digitalWrite(RFM95_RST, HIGH);
  delay(10);

  while (!rf95.init()) {
    Serial.println("LoRa radio init failed");
    while (1);
  }
  Serial.println("LoRa radio init OK!");

  // Defaults after init are 434.0MHz, modulation GFSK_Rb250Fd250, +13dbM
  if (!rf95.setFrequency(RF95_FREQ)) {
    Serial.println("setFrequency failed");
    while (1);
  }
  Serial.print("Set Freq to: "); Serial.println(RF95_FREQ);

  // Defaults after init are 434.0MHz, 13dBm, Bw = 125 kHz, Cr = 4/5, Sf = 128chips/symbol, CRC on

  // The default transmitter power is 13dBm, using PA_BOOST.
  // If you are using RFM95/96/97/98 modules which uses the PA_BOOST transmitter pin, then
  // you can set transmitter powers from 5 to 23 dBm:
  rf95.setTxPower(23, false);
}

int16_t packetnum = 0;  // packet counter, we increment per xmission

void loop()
{
  int x = 0;
  state = !(digitalRead(BUTT1));
  while (x < 4) {
    state = !(digitalRead(BUTT1));
    digitalWrite(13, state);
    int flow = checkFlow(x);
    transmitBait(x, state, flow);
    delay(400); // Wait 1 second between transmits, could also 'sleep' here!
    x++;
  }
  delay(5000);
}


//Sends to the bait number (0-3), selects the state (0/off 1/on), selects flow setting (0-9)

void transmitBait(int baitnum, int state, int flow) {
  digitalWrite(13, HIGH);
  Serial.println("Transmitting..."); // Send a message to rf95_server
  String sendStr = String(baitnum);
  sendStr += ",";
  sendStr += String(state);
  sendStr += ",";
  sendStr += String(flow);
  Serial.print("Sending "); Serial.println(sendStr);
  char sendBuf[6];
  sendStr.toCharArray(sendBuf, 6);
  Serial.println("Sending...");
  delay(10);

  rf95.send((uint8_t *)sendBuf, sizeof(sendBuf));

  Serial.println("Waiting for packet to complete...");
  delay(10);
  rf95.waitPacketSent();
  // Now wait for a reply
  uint8_t buf[RH_RF95_MAX_MESSAGE_LEN];
  uint8_t len = sizeof(buf);

  Serial.println("Waiting for reply...");
  if (rf95.waitAvailableTimeout(400))
  {
    // Should be a reply message for us now
    if (rf95.recv(buf, &len))
    {
      digitalWrite(tLED[baitnum], HIGH);
      Serial.print("Got reply: ");
      Serial.println((char*)buf);
      state = buf[2] - 48;

      //int flowSetting = buf[4] - 48;
      digitalWrite(sLED[baitnum], state);
      Serial.print("RSSI: ");
      Serial.println(rf95.lastRssi(), DEC);
      digitalWrite(tLED[baitnum], LOW);
    }
    else
    {
      Serial.println("Receive failed");
    }
  }
  else
  {
    Serial.println("No reply, is there a listener around?");
  }
  digitalWrite(13, LOW);



}

byte checkMuxPin(int pin, int bank) {
  for (int i = 0; i < 4; i++) {
    byte state = bitRead(pin, i);
    digitalWrite(s[i], state);
    //Serial.print(state);
  }
  //Serial.print(",");
  //Serial.println(pin);
  byte check = digitalRead(bank);
  return check;
}

int checkFlow(int bait) {
  int setting = 0;
  for (int i = 0; i < 10; i++) {
    byte val = checkMuxPin(i, b[bait]);
    if (val == 0) {
      setting = i;
    }
  }
  //Serial.print("Flow Setting: ");
  //Serial.println(setting);
  return setting;
}
